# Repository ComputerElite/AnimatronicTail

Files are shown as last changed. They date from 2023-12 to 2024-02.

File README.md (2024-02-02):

# Animatronic Tail by ComputerElte
This is a project for an animatronic tail with LEDs

# Contact
`computerelite` on Discord or open an issue on this repo. If you know me personal message me on Telegram.

# Project roadmap (personal tail)
* [x] Replace 30led/m strip with 60 or 144led/m strip (Tip: Check that your cables are thick enough for more leds)
* [x] Add fur covering (which still lets light through)
* [ ] Add IMU for cool movement sync stuff
* [ ] Save custom animations in backend (or frontend if lazy)

# Videos and Pictures
ToDo 

# Building the tail
*As of 2023/12/16*
## Background
I saw animatronic tails by the tail company and said "yeah I can do that too".

## Parts
Sourced from Ebay, Hornbach, local shops and my local makerspace
#### Required
- 3d printer with enough PLA (around 500g should be sufficient)
- High torque servos (I used 30kg cm servos. I ordered 270° but 180° arrived which is still enough https://www.ebay.de/itm/295910063432)
- About 80-90cm of 6mm wire rope https://www.hornbach.de/p/drahtseil-poesamo-o-6-mm-stahl-verzinkt-meterware/5002820/
- ESP 8266 (you could also use an ESP 32 if you want to add more stuff)
- Fishing wire (used to actuate the tail. Thin Wire ~1.5mm-3mm may be a better choice here)
- Tape
- M3 screws in various lengths, washers, nuts and [threads](https://www.amazon.de/Gewindeeinsatz-Einpressmutter-Gewindebuchsen-Kunststoff-Box-Kunststoffteiledurch/dp/B09B7F2XM3/)

#### Optional
- USB C port for power https://www.ebay.de/itm/284920406558
- 1m WS2812 LED strip for lights! Preferrably 60led/m or more https://www.ebay.de/itm/374479289527

## Printing required parts
### Info
In a lot of finished prints I had to widen holes, add extra holes or hone down openings

### Segments for the tail
You can find files for the tail segments in stl/TailSegments. The file name is the diameter. Files ending in `_mounting` have mounting holes for screwing them to the case.

*If you need the CAD files ask me with a preferred format and I'll put them into the repo if possible.*

You can print as many as you want, usually in descending size but you can choose whatever you want. e. g. I printed 100m, 100mm, 90mm, 80mm, 70mm, 60mm, 50mm iirc.
After printing you'll have to [put M3 threads into the holes](https://www.youtube.com/shorts/iw2qNMok5ok). The big hole in the middle is for the wire rope, the small one at the side is for the M3 thread.
After inserting the thread you can secure the Tail segment.

### Case
The case can be printed as is. It has holes for the servos, the tail segment mount and, cable management and a belt.

### Belt holder extender (Optional)
This is an extension for the backplate of the case so it doesn't bend down as much. I experienced that the servo wheels slid on my ass so I made that extension.
Print `BeltHolderHolder.stl` once and `BeltHolderHolderHolder.stl` twice.

### Servo wheels
There are wheels which attach to the servos. The wire for pulling on the tile will be fastened to them. They are tailored to the servos I ordered.
One M3 screw simultaniously attaches the wheel to the servo and holds the wire for pulling the tail.

## Electronics
Electronics were soldered by hand with a hole plate.

### ESP8266
Create a board which has power in and ground. That is connected to the ESP VIN and GND pin. The servos and leds are also connected with the Power in as well as Data pins on the ESP.
I used header pins for easily connecting and disconnecting the parts.

## Assembly
### Assembling the tail part
Take your printed tail segments and screw them to the wire rope in roughly same spacing

### Assembling the case
Assembling the case is the hardest part as everything is hard to reach

1. Secure the tail part to the mounting holes with 4 screws, washers and nuts (secure everything like this unless explicitly stated otherwise or your know better).
2. Secure the belt holder extender by clamping the BeltHolderHolder to the back of the case with both BeltHolderHolderHolders. Simply use M3 screws and nuts to tighten everything equally all the way.
3. Secure the servos with 4 screws each. They should be inserted from the inside.
4. Connect all the electronics and power it on. The tail should return to its default position.
5. Secure the servo arms to the servo pointing to the top.
6. Screw the servo wheel in but not all the way.
7. Thread the wire through all holes in the tail segments then through the top hole of the servo wheel. Wrap it around the screw in the middle a few times and then tighten the screw holding the servo wheel on the servo.
   This will securely hold the wire in (more or less).
8. Bend the tail slightly upward while on your table. Then secure the wire with a triple knot (or more) on the other end of the tail. Both sides should have the same tension.
   Tension should be the highest when it's laying flat on your table.
9. Secure all electronics with tape and manage your cables.

I am aware that this isn't a complete guide. I will expand it if questions arise. However by modifying the code in some places you should have a working tail now.

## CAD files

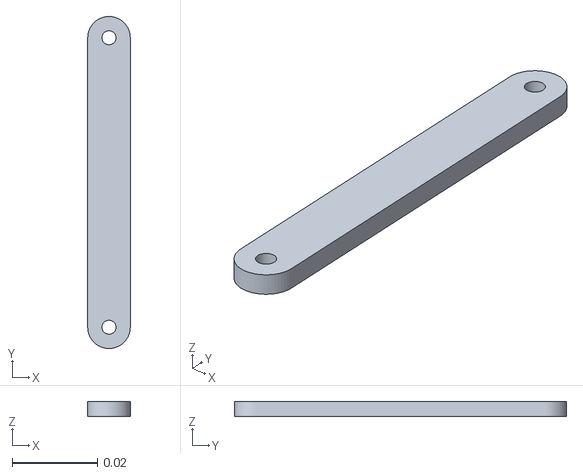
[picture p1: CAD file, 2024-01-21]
stl/BeltHolderHolderHolderV3.stl
0.01 x 0.078 x 0.0035

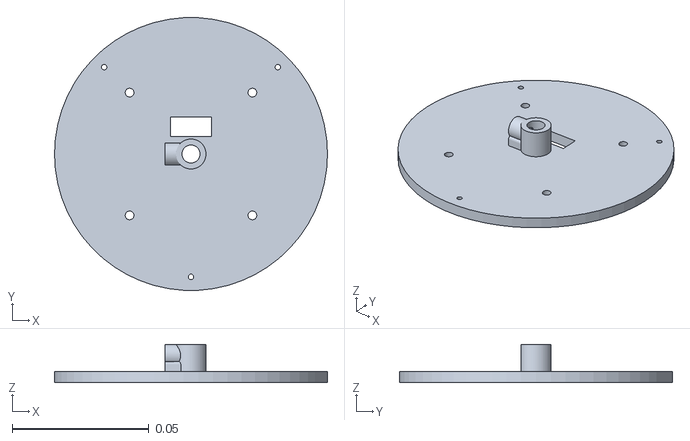
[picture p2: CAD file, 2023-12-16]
stl/TailSegments/100mm_mounting.stl
0.1 x 0.0999 x 0.014

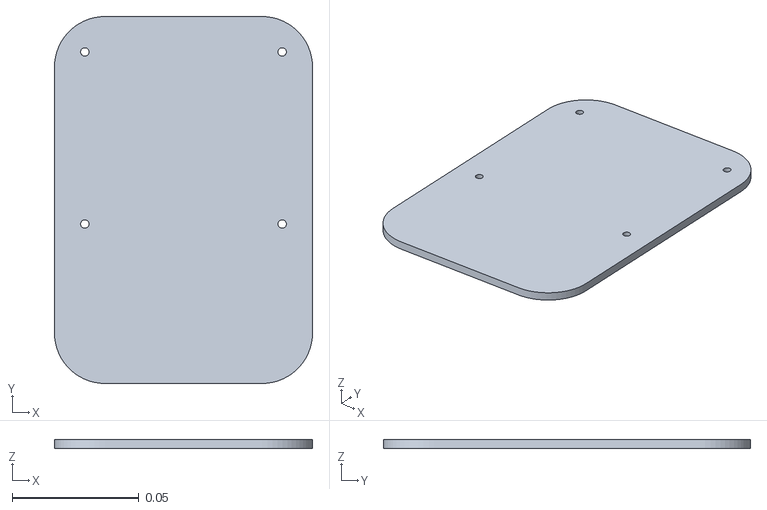
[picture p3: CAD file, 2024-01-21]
stl/BeltHolderHolderV5.stl
0.102 x 0.145 x 0.0035

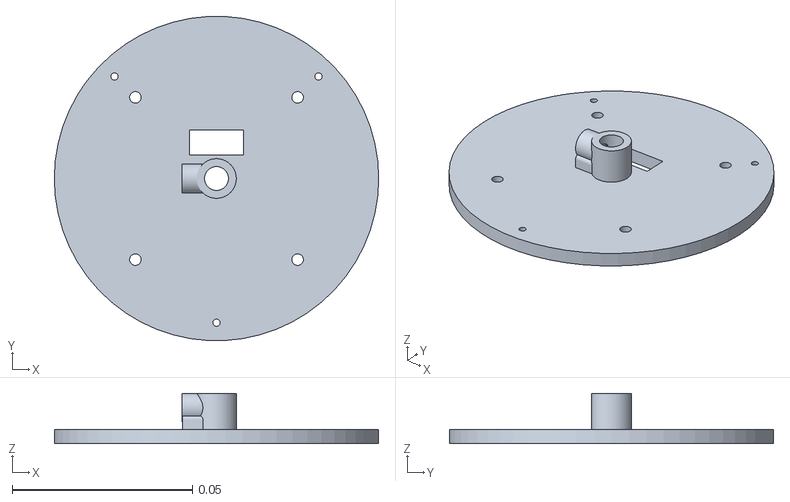
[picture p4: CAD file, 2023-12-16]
stl/TailSegments/90mm_mounting.stl
0.09 x 0.0899 x 0.014

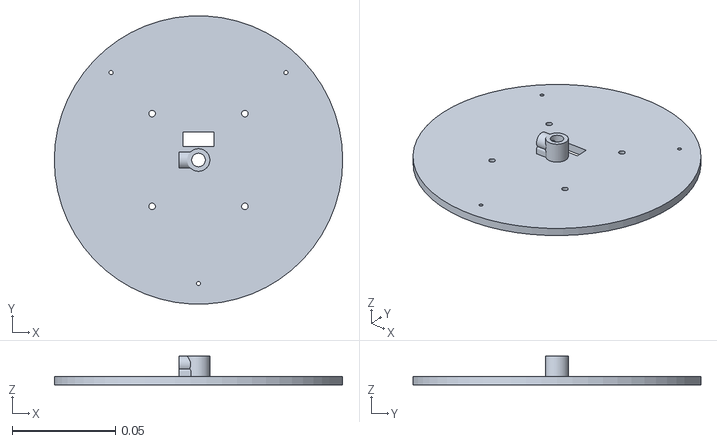
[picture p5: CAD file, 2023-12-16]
stl/TailSegments/140mm_mounting.stl
0.14 x 0.14 x 0.014

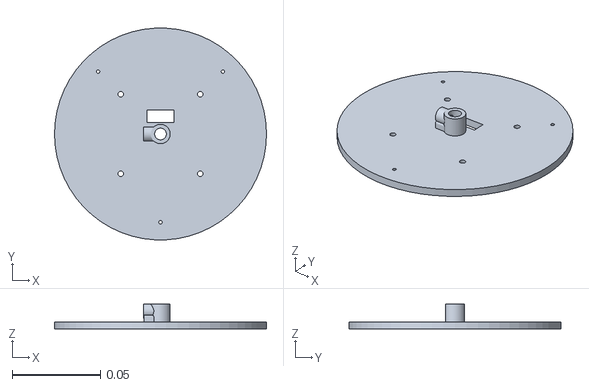
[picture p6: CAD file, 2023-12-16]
stl/TailSegments/120mm_mounting.stl
0.12 x 0.12 x 0.014

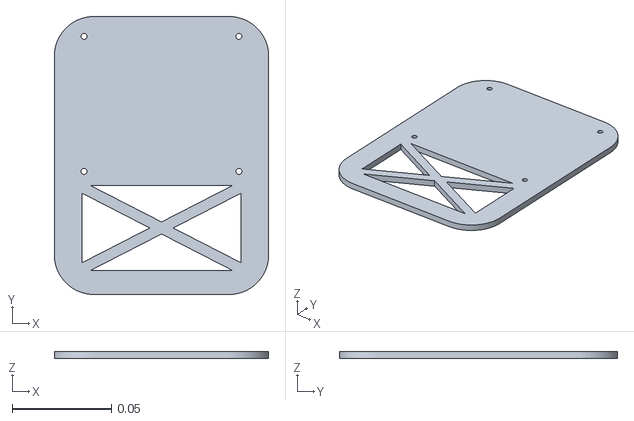
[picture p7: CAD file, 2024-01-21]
stl/BeltHolderHolderNewNew.stl
0.108 x 0.14 x 0.0035

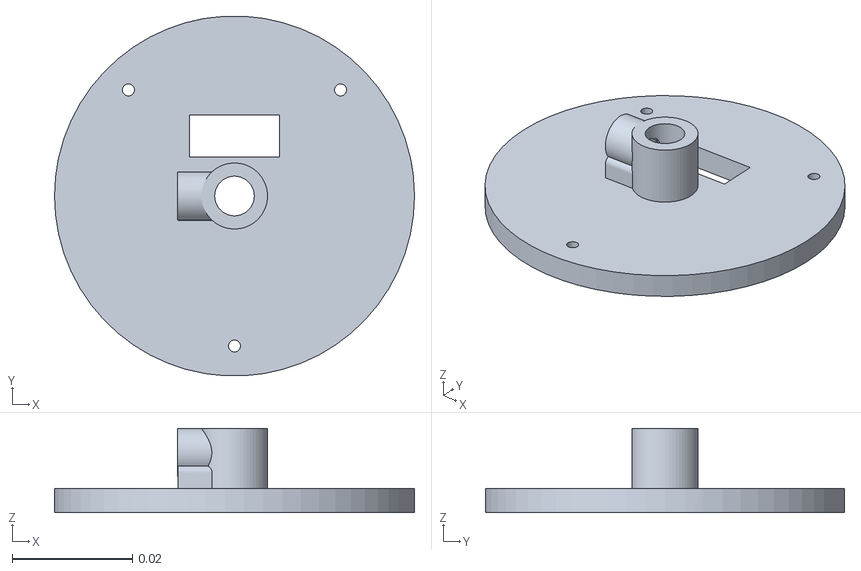
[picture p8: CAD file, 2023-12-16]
stl/TailSegments/60mm.stl
0.06 x 0.0599 x 0.014

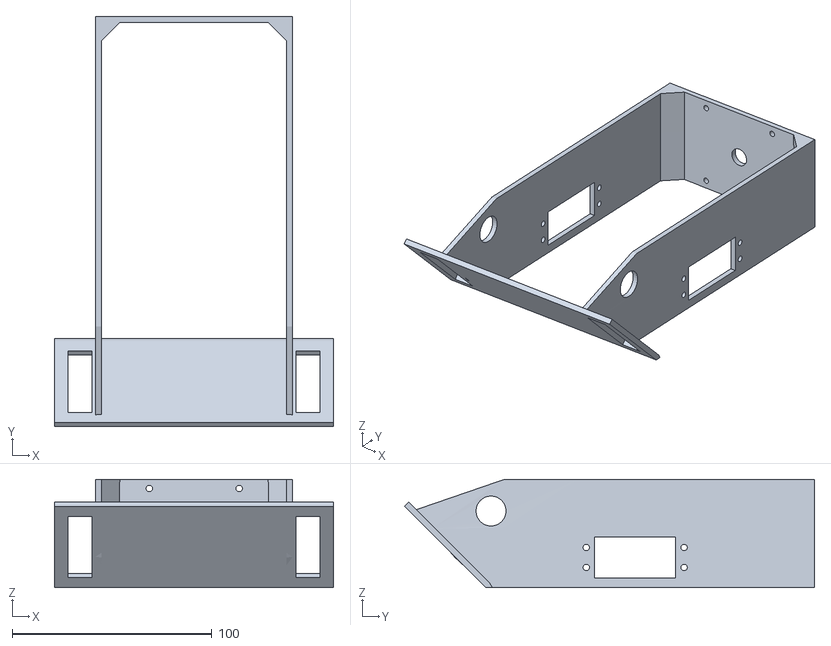
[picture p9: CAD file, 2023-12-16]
stl/Case.stl
140.0 x 205.4 x 54.3

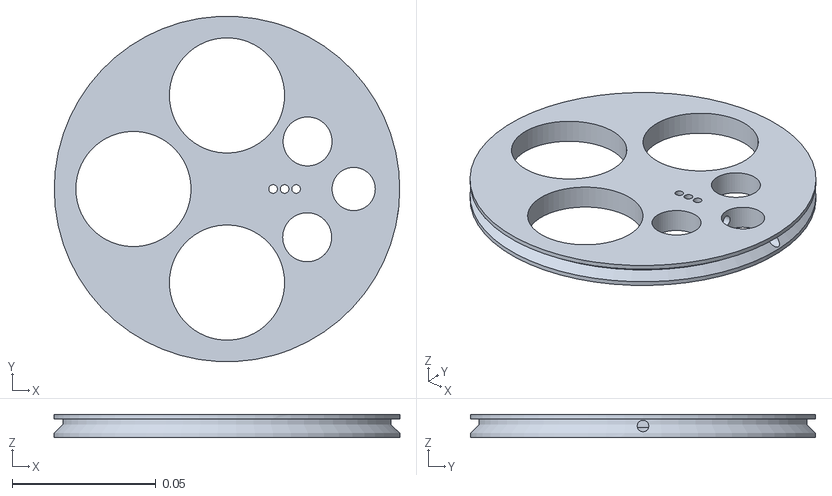
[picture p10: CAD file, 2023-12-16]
stl/ServoWheel.stl
0.12 x 0.12 x 0.008

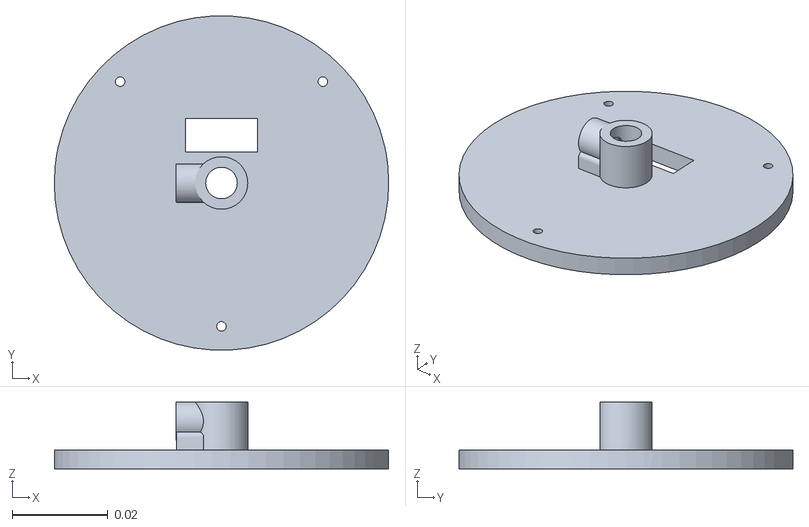
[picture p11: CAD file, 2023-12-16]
stl/TailSegments/70mm.stl
0.07 x 0.0699 x 0.014

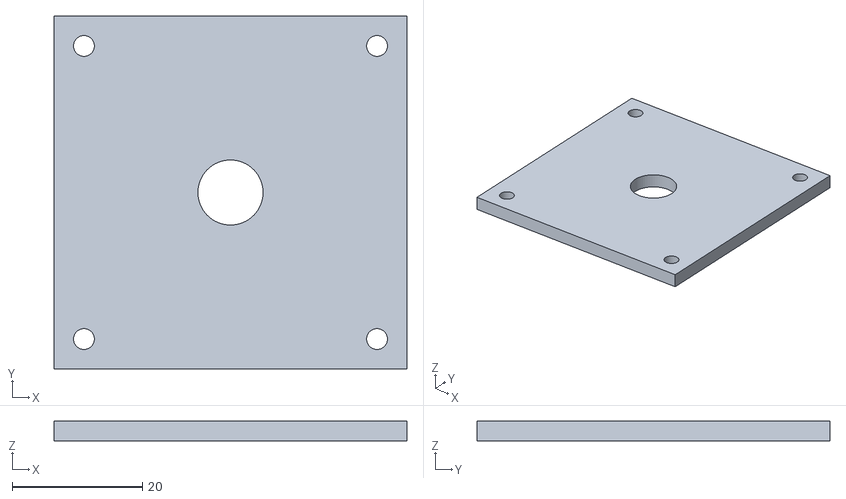
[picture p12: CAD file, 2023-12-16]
stl/MountingPlateThinn.stl
54.2 x 54.2 x 3.00

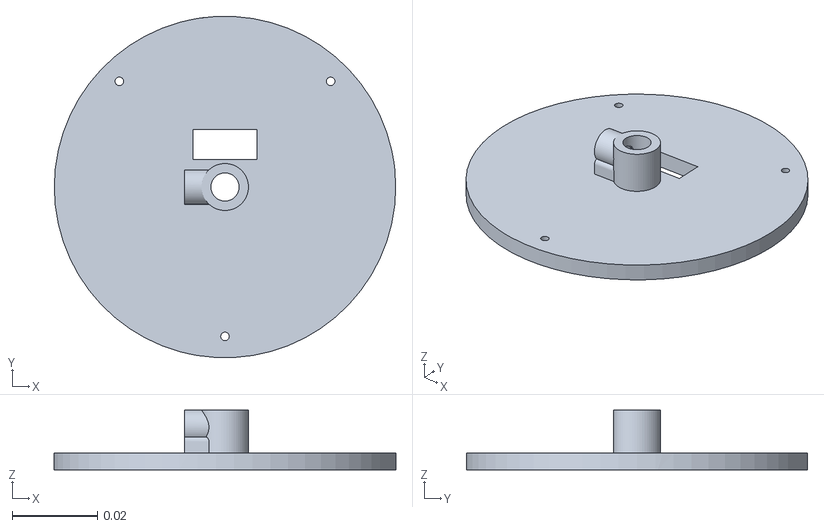
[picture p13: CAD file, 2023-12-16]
stl/TailSegments/80mm.stl
0.08 x 0.0799 x 0.014

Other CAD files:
stl/TailSegments/120mm.stl
stl/BeltHolderHolderNew.stl
stl/TailSegments/100mm.stl
stl/TailSegments/90mm.stl
stl/TailSegments/140mm.stl
stl/BeltHolderHolder.stl
stl/BeltHolderHolderHolder.stl
stl/BeltHolderHolderHolderV2.stl
stl/BeltHolderHolderV4.stl
stl/BeltHolderThinn.stl
stl/Case.blend
stl/TailSegments/40mm.stl
stl/TailSegments/50mm.stl

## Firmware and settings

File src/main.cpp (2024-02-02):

#define VRX_PIN A2
#define VRY_PIN A1
#include <FastLED.h>
#include "leds.h"
#include "preferences.h"
#include "wifi.h"
#include "server.h"
#include "animations.h"
#include "main.h"
#include "bluetooth.h"

double deltaTimeSeconds = 0;
long deltaTime = 0;
long lastLoop = 0;


void setup() {
  Serial.begin(9600);
  FastLED.addLeds<WS2812B, LED_PIN>(ledsRGB, getRGBWsize(N_LEDS));
  SetLED(LEDAnimation::WIFI_CONNECTING);
  LoadPreferences();
  //if(ShouldResetPreferences()) ResetPreferences(false);
  BeginWifi();
  BeginServos();
  //Serial.print("Soft-AP IP address = ");
  //Serial.println(WiFi.softAPIP());

  SetupServer();
  //SetupBluetooth();
  RestartServer();
}




void PrintDebug() {
  Serial.print("D: ");
  Serial.print(deltaTime);
  Serial.print(" L: ");
  Serial.print(map((long)(percentageL * 10), 0, 1000, 500, 2500));
  Serial.print(" R: ");
  Serial.print(map((long)(percentageR * 10), 0, 1000, 2500, 500));
  Serial.print(" T: ");
  Serial.print(targetPercentageL);
  Serial.print(" ");
  Serial.println(targetPercentageR);
}

void loop() {
  deltaTime = millis() - lastLoop;
  deltaTimeSeconds = static_cast<double>(millis() - lastLoop) / 1000.0;
  lastLoop = millis();
  HandleAnimation();
  //PrintDebug();
  HandleLEDS();
  HandleWifi();
  HandleServos();
  //HandleBluetooth();
  delay(5);
}

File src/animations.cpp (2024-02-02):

#include "animations.h"
#include "main.h"
#include <ESP32Servo.h>
#include "preferences.h"

double percentageL = 0;
double percentageR = 0;
double targetPercentageL = 20;
double targetPercentageR = 20;

int currentAnimation = 0;

int currentAnimationStep = 0;
bool animationStepComplete = false;

#define X(a, name, speed, group) name,
char const *tail_animation_names[] =
{
    TAIL_ANIMATIONS
};
#undef X

#define X(a, name, speed, group) group,
int const tail_animation_groups[] =
{
    TAIL_ANIMATIONS
};
#undef X

#define X(a, name, speed, group) speed,
int const tail_animation_speeds[] =
{
    TAIL_ANIMATIONS
};
#undef X

double percentPerSecond = 35;

bool oneShot = false;

int TAIL_POS_0 = 0;
int TAIL_POS_LOW = 20;
int TAIL_POS_MID = 55;
int TAIL_POS_HIGH = 70;

int GetAnimation() {
  return currentAnimation;
}

void SetAnimation(int animation) {
  currentAnimation = animation;
  SaveAnimation(currentAnimation);
  currentAnimationStep = 0;
  animationStepComplete = true;
}

void SetSpeed(int speed) {
  percentPerSecond = speed;
  SaveSpeed(speed);
}
int GetSpeed() {
  return percentPerSecond;
}

void HandleAnimation() {
  if(animationStepComplete) {
    currentAnimationStep++;
    animationStepComplete = false;
  }

  switch (currentAnimation)
  {
  case REST_LOW:
    // Stop tail
    targetPercentageL = TAIL_POS_0;
    targetPercentageR = TAIL_POS_0;
    break;


  case V_WAG:
    // go to default pos
    switch (currentAnimationStep)
    {
    case 0:
      targetPercentageL = TAIL_POS_LOW;
      targetPercentageR = TAIL_POS_LOW;  
      break;
    case 1:
      targetPercentageL = TAIL_POS_MID;
      targetPercentageR = TAIL_POS_LOW;  
      break;
    case 2:
      targetPercentageL = TAIL_POS_LOW;
      targetPercentageR = TAIL_POS_LOW;  
      break;
    case 3:
      targetPercentageL = TAIL_POS_LOW;
      targetPercentageR = TAIL_POS_MID;  
      break;
    default:
      if(oneShot) currentAnimation = 0;
      else {
        currentAnimationStep = 0;
        animationStepComplete = false;
        HandleAnimation();
      }
      break;
    }
    break;


  case WAG:
    switch (currentAnimationStep)
    {
    case 0:
      targetPercentageL = TAIL_POS_LOW;
      targetPercentageR = TAIL_POS_MID;  
      break;
    case 1:
      targetPercentageL = TAIL_POS_MID;
      targetPercentageR = TAIL_POS_LOW;  
      break;
    default:
      if(oneShot) currentAnimation = 0;
      else {
        currentAnimationStep = 0;
        animationStepComplete = false;
        HandleAnimation();
      }
      break;
    }
    break;
  case EXCITED_WAG:
    switch (currentAnimationStep)
    {
    case 0:
      targetPercentageL = TAIL_POS_MID;
      targetPercentageR = TAIL_POS_MID - 20;  
      break;
    case 1:
      targetPercentageL = TAIL_POS_MID - 20;
      targetPercentageR = TAIL_POS_MID;  
      break;
    default:
      if(oneShot) currentAnimation = 0;
      else {
        currentAnimationStep = 0;
        animationStepComplete = false;
        HandleAnimation();
      }
      break;
    }
    break;

  case UP_AND_DOWN:
    switch (currentAnimationStep)
    {
    case 0:
      targetPercentageL = TAIL_POS_LOW;
      targetPercentageR = TAIL_POS_LOW;  
      break;
    case 1:
      targetPercentageL = TAIL_POS_MID;
      targetPercentageR = TAIL_POS_MID;  
      break;
    default:
      if(oneShot) currentAnimation = 0;
      else {
        currentAnimationStep = 0;
        animationStepComplete = false;
        HandleAnimation();
      }
      break;
    }
    break;
  case REST_MID:
    targetPercentageL = TAIL_POS_MID;
    targetPercentageR = TAIL_POS_MID;
    break;
  case REST_HIGH:
    targetPercentageL = TAIL_POS_HIGH;
    targetPercentageR = TAIL_POS_HIGH;
    break;
  case CIRCLE:
    switch (currentAnimationStep)
    {
    case 0:
      targetPercentageL = TAIL_POS_LOW;
      targetPercentageR = TAIL_POS_LOW;  
      break;
    case 1:
      targetPercentageL = TAIL_POS_LOW;
      targetPercentageR = TAIL_POS_MID;  
      break;
    case 2:
      targetPercentageL = TAIL_POS_HIGH;
      targetPercentageR = TAIL_POS_HIGH;  
      break;
    case 3:
      targetPercentageL = TAIL_POS_MID;
      targetPercentageR = TAIL_POS_LOW;  
      break;
    default:
      if(oneShot) currentAnimation = 0;
      else {
        currentAnimationStep = 0;
        animationStepComplete = false;
        HandleAnimation();
      }
      break;
    }
    break;

  default:
    currentAnimation = 0;
    break;
  }
}

Servo left;
Servo right;

void SetL(double percentage) {
  left.writeMicroseconds(map((long)(percentage * 10), 0, 1000, 500, 2500));
}
void SetR(double percentage) {
  right.writeMicroseconds(map((long)(percentage * 10), 0, 1000, 2500, 500));
}
void BeginServos() {
  left.attach(SERVOL_PIN);
  right.attach(SERVOR_PIN);
  SetL(percentageL);
  SetR(percentageR);
}
void HandleServos() {
    if(targetPercentageL < percentageL) {
    percentageL -= percentPerSecond * deltaTimeSeconds;
    if(percentageL < targetPercentageL) {
      percentageL = targetPercentageL;
    }
  } else if(targetPercentageL > percentageL) {
    percentageL += percentPerSecond * deltaTimeSeconds;
    if(percentageL > targetPercentageL) {
      percentageL = targetPercentageL;
    }
  }

  if(targetPercentageR < percentageR) {
    percentageR -= percentPerSecond * deltaTimeSeconds;
    if(percentageR < targetPercentageR) {
      percentageR = targetPercentageR;
    }
  } else if(targetPercentageR > percentageR) {
    percentageR += percentPerSecond * deltaTimeSeconds;
    if(percentageR > targetPercentageR) {
      percentageR = targetPercentageR;
    }
  }

  if(percentageL == targetPercentageL && percentageR == targetPercentageR) {
    animationStepComplete = true;
  }


  SetL(percentageL);
  SetR(percentageR);
}

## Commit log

2023-11-25 Servo code
2023-12-01 Can't fix hardware issues with software :(
    [main.cpp]
2023-12-02 update wheel size
2023-12-16 Add stl and blend files
    [100mm.stl, 120mm.stl, 140mm.stl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]
2023-12-16 add belt holder
    [100mm_mounting.stl, 120mm_mounting.stl, 140mm_mounting.stl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]
2024-01-21 Add new belt holder holder design
    [BeltHolderHolderNewNew.stl]
2024-01-21 Change holes from 3mm to 3.3mm
    [BeltHolderHolderHolderV3.stl]
2024-02-02 Upgrade to ESP 32, custom animations, idfk, failed attempt at bluetooth
    [animations.cpp, bluetooth.cpp, leds.h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]
